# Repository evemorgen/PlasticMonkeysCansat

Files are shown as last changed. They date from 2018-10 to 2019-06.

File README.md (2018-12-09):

# Welcome to Plastic Monkeys - Emergency Beacan repo

Emergency beacan cad render

This is the place where we keep all our work related to Emergency Beacan project.

We are building a CanSat (CanSat is a small soda-sized piece of electronics, created to conduct a scientific mission) equiped with multiple sensors, radio, GPS, thermal camera and screen to provide communication to the victims of natural disasters. Usually, after an earthquake or tsunami, big expeditions and rescue operations take place. Unfortunately they are very often dangerous for rescuers and very expensive. We came up with a solution - instead of people, we can send there many small sats, anyone who finds them can easily send their localization to the rescue center and have a short interview. 

----

## Repo structure

Emergency Beacan is multidisciplinary project involving software, electronics, mechanical design and so on. That being said, there are couple directories covering all mentioned before:

  - [`code`](code/) - keeps all software related stuff
  - [`docs`](docs/) - is the place where we keep project documentation, you might be espetialy interested in our [reports](docs/reports)
  - [`assets`](assets/) - contains all graphical designs regarding our logos and .. assets?
  - [`diagrams`](diagrams/) - all things related to visual representation of conceptual design

----

## Where to find us

We are present in most of modern social media platforms, you can follow us at:
  - our website <http://plastic-monkeys.space>
  - [facebook](https://www.facebook.com/pmcansat/)
  - [instagram](https://www.instagram.com/pmcansat/)
  - [youtube](https://www.youtube.com/channel/UCQk3wuW7xEt5WVLtaiRNTGQ)
  - or write us old fashioned email <hello@plastic-monkeys.space>

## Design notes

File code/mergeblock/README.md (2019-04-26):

# Easy Merge Block

### How to use:
in config.ini specify your settings:  
`output` = path to file where binary ready-to-send packets are going to be stored, will be created if it doesn't exist  
`datalog` = path to file where readable packets are going to be stored, will be created if it doesn't exist  
`sleeptime` = delay before merges  
`line_length` = your maximum line length in sensors' logs - how many bytes script have to load to RAM to load last line  
`text_packets` = yes or no - set to yes if you want to have readable packets  
`exception_sleep_time` = delay after getting an exception  
`packet_length` = number of bytes in output packet  

You also specify paths to all logs that we want to merge in `[PATHS]` section like this:
```
[PATHS]
path1 = foo1.log
path2 = /home/xyz/Desktop/foo2.log
path3 = /home/sensors/temperature/temp.log
```

### Output:
Packet of `packet_length` size in `bytes`:  
one byte describing data_dict size + msgpacked data_dict + fill ('-') to `packet_length`  

### Start:
Next you can run your mergeblock using: `python3 merge.py`  
Libraries used: configparser, msgpack, time, sys, re, logging

### Some additional notes:
Mergeblock takes only last int from sensors' logs' lines: when we have line like this:  
`123 255`  
mergeblock will use only 255 as our value. This approach gives us the ability to add things like timestamps to each reading, that will be ignored by mergeblock, but can be useful after retrieving sd_card with sensors' logs.

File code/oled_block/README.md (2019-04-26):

# OLED_BLOCK

### Get this bad boy working:  
Just follow [this](https://www.raspberrypi-spy.co.uk/2018/04/i2c-oled-display-module-with-raspberry-pi/) tutorial.

### How it works?
Program should have access to oled_buffer.txt file, you can specify the path in the config file.  
It reads a file and converts it into string, ignoring new lines (`'\n'`) and "fillers" (`'-'`).  
After that it splits a message into lines, you can define width of them in config file (recommend 20 for 0.96 inch OLEDs), and prints them.  
It also adds hyphens where it's necessary.  
It repeats the process, with delay equal to `sleep_time` variable specified in config file

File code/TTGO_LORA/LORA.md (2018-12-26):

# LoRa w/ TTGO

Hello, here are some notes about our RaO2 working with TTGO.

## TTGO SETUP

Firstly - our TTGO from Germany is actually called Heltec WiFi LoRa 32

To start working with it you need to add some libraries, it is shown in steps below:

#### Step 1
Erase all old ESP32 Libraries that you've installed before. If you haven't you can skip this step.

#### Step 2
Jump to Arduino IDE, go to File > Preferences > Additional Board Manager URLs, add this line:
`https://dl.espressif.com/dl/package_esp32_index.json`

#### Step 3
Jump to Tools > Boards > Board Manager and search ESP32, next download:
`esp32 by Espressif Systems`

#### Step 4
Go to Library Manager (Open Sketch > Include Library > Manage Libraries) and install:
`LoRa by Sandeep Mistry`

#### Step 5
Install another library from Libraries Manager:
`U8g2`

Alternative Link: [U8g2](https://github.com/olikraus/u8g2)

#### Step 6

Go to Boards and select:
`Heltec_WIFI_LoRa_32`

#### That's it!

## LORA NOTES

In my configuration (Arduino Micro with Ra02 as a TX, Heltec Board as a receiver) it works with best results with:

#### TX
```LoRa.setSpreadingFactor(7)
LoRa.setTxPower(20); //TX Power
int delayTime = 100; //Time between sending packets
```

Coding Rate and Spreading Factor are responsible for data transfer speed. However Coding Rate is set to the best value
By default, Spreading factor is the better the lower. Unfortunately as you can read here: [LoRa Library API](https://github.com/sandeepmistry/arduino-LoRa/blob/master/API.md)
Spreading Factor lower than 7 requires an implicit header mode. You can start it by:
`LoRa.beginPacket(implicitHeader);`

But then TTGO (RX) starts to loose about half of packets, making data transfer actually worse than with Sprading Factor = 7.
Also the BAND 433E6 is the best one && LoRa with Arduino needs around 1A power supply to provide the best results.

I didn't change anything in RX, there's not much to tinker around. It just mustn't clear the display very often - it is so slow,
that TTGO misses all packets during this proccess. What's important about TTGO is that its OLED run on SPI, pinout is
pretty weird and writing code for OLED Screen from scratch can be quite hard. I strongly suggest using code that is in this repo.

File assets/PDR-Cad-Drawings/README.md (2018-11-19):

# Images provided with files:  
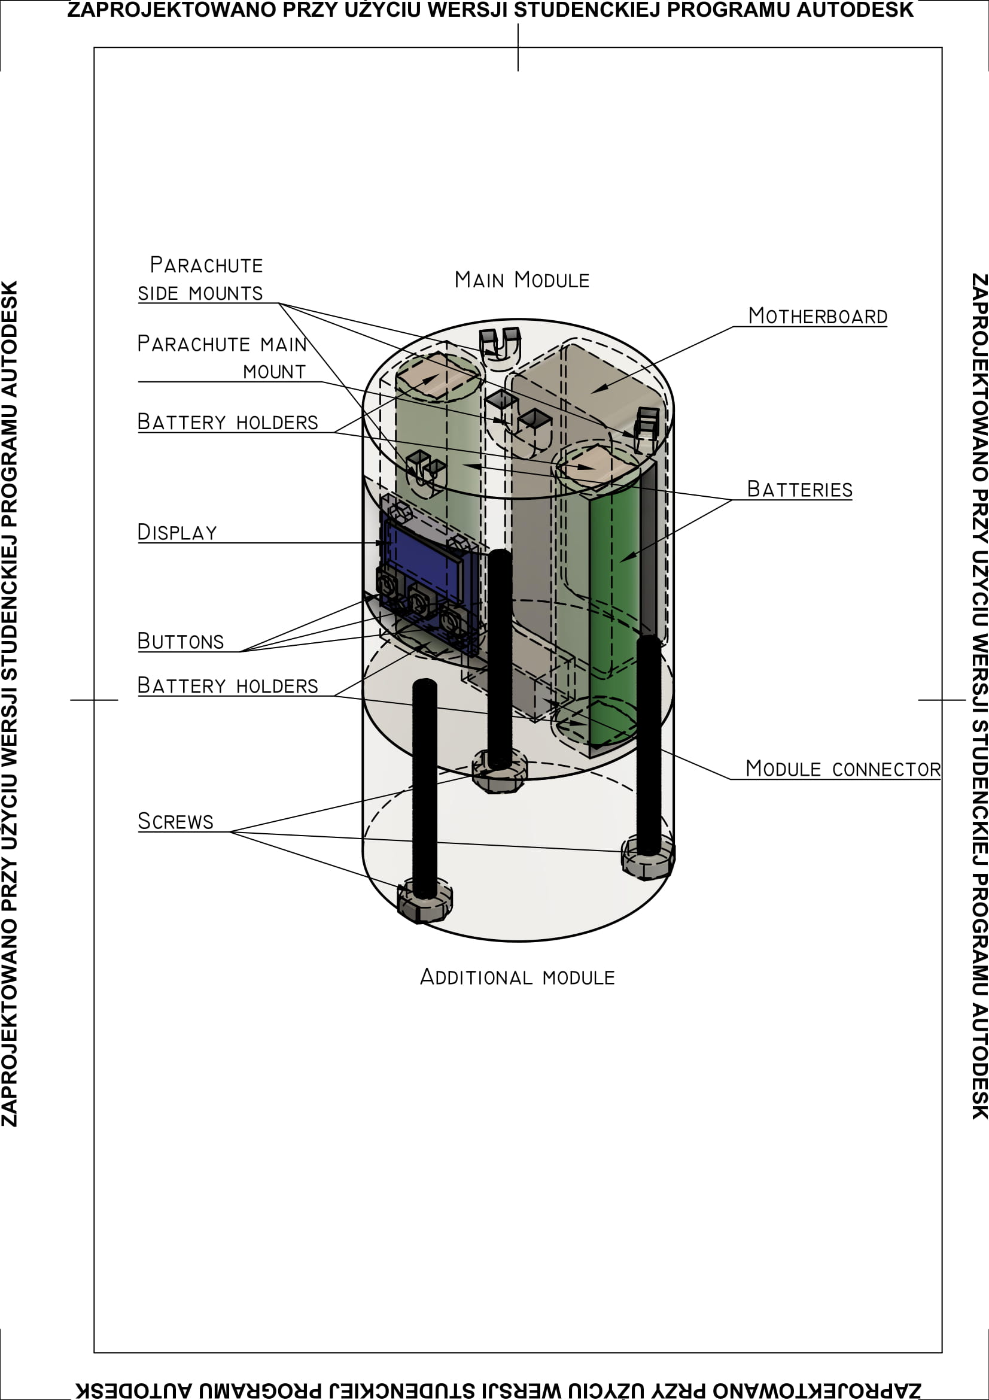
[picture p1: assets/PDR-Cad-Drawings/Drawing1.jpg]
  
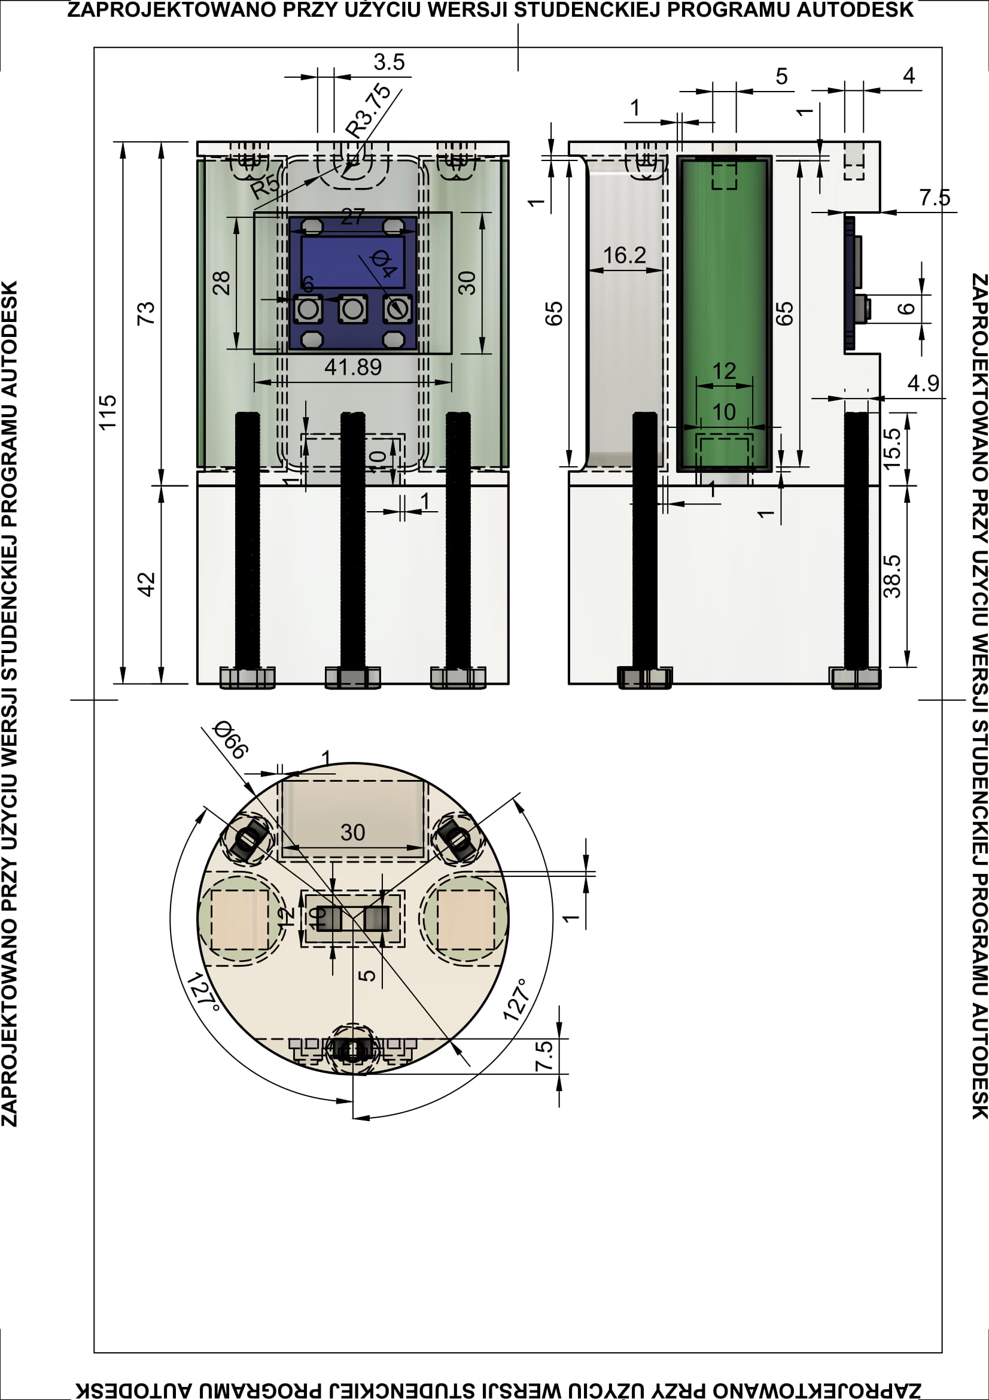
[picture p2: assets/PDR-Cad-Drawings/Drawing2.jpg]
  
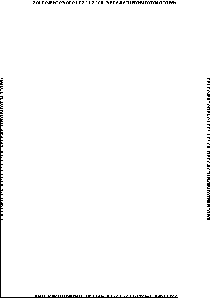
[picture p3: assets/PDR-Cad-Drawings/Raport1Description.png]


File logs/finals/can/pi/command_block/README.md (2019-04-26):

# Command Block

#### Requirements:
  Needs config.ini with specified:  
  `camera_log_file` - file where photos' timestamps appear  
  `thermal_log_file` - file where thermal photos' timestamps appear  
  `oled_text_buffer` - file from which the text will be read on OLED, and where we will append text  
  `lora_status_file` - file where lora commands will appear  
  `rx_file` - file with recieved string-packets to process  
  `sleep_time` - delay time in seconds (float) between processing new messages  
  `exception_sleep_time` - delay time in seconds (float) after getting a exception  
  `packet_line_length` - length of a packet, at least 7  
  `time_stamp_length` - number of characters used in packet to describe a timestamp  

  ##### Note:
  First character in each packet should be a one char header!

#### How it works:
  Each sleep_time command_block reads the recent recieved packet from the rx_file if new line popped in. After that it analyzes the first charachter (line[0]) in the packet. Afterwards, it runs a adequate function.
  
#### Command headers:

  ##### I
  Request for a regular image from camera. Requires a destinated timestamp at `line[1]` - `line[timestamp_length]` and quatlity at `line[timestamp_length+1]`
  ##### T
  Request for a thermal image from camera. Requires a destinated timestamp at `line[1]` - `line[timestamp_length]`  
  ##### R
  Checks `line[0]` - `line[5]` for `'REBOOT'` command. Request for a reboot. Requires command_block running as a root
  ##### S
  Request for a system info. Sends back cpu usage, battery percentage, free disk space
  ##### A
  Appends text from a packet from `line[1]` to `line[packet_line_length-1]` to oled Screens buffer.
  ##### C  
  Clears oled buffer

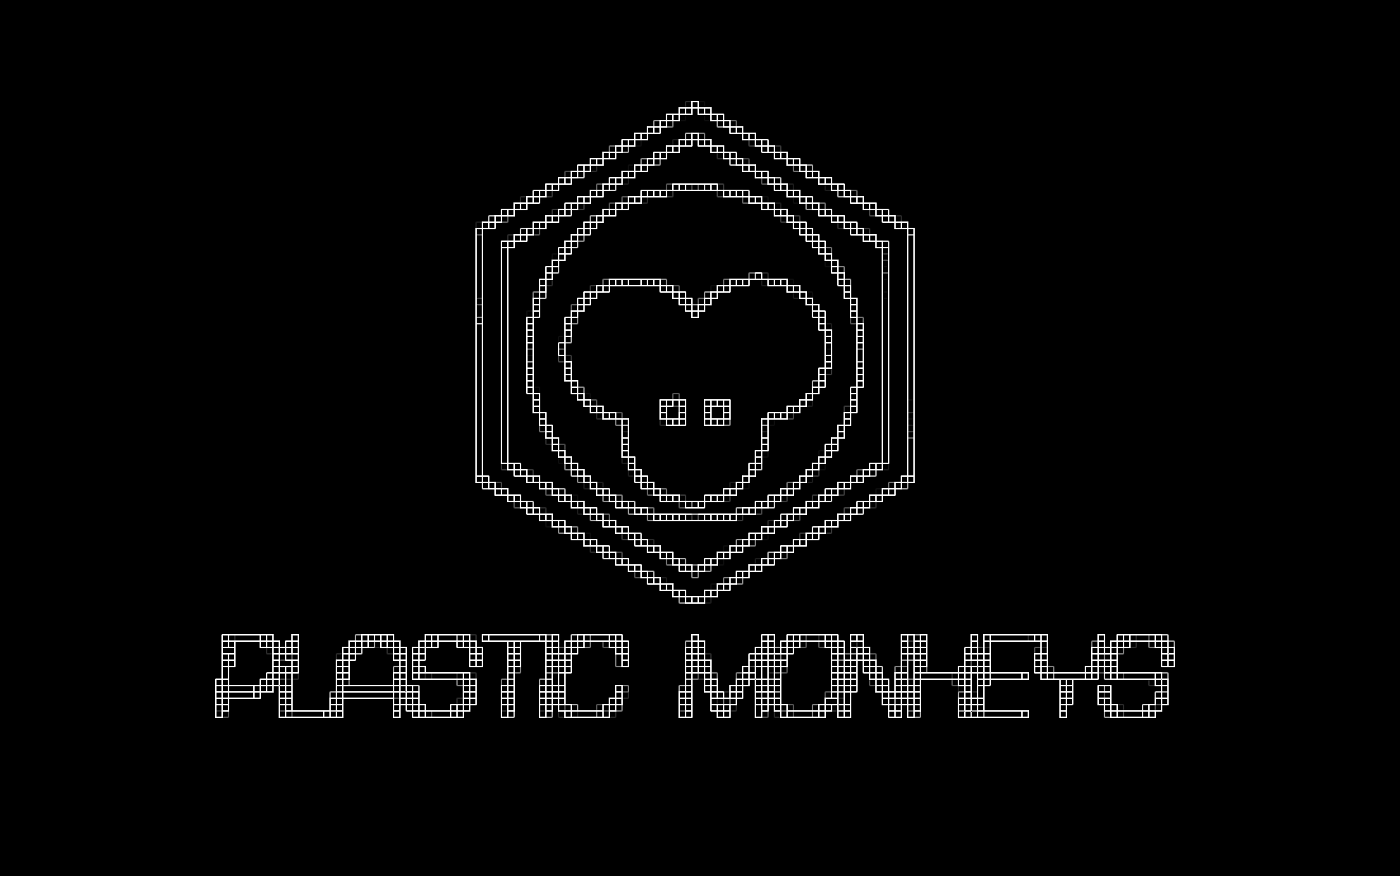
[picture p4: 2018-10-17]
assets/wallpaper-graphics/wallpaper2.png

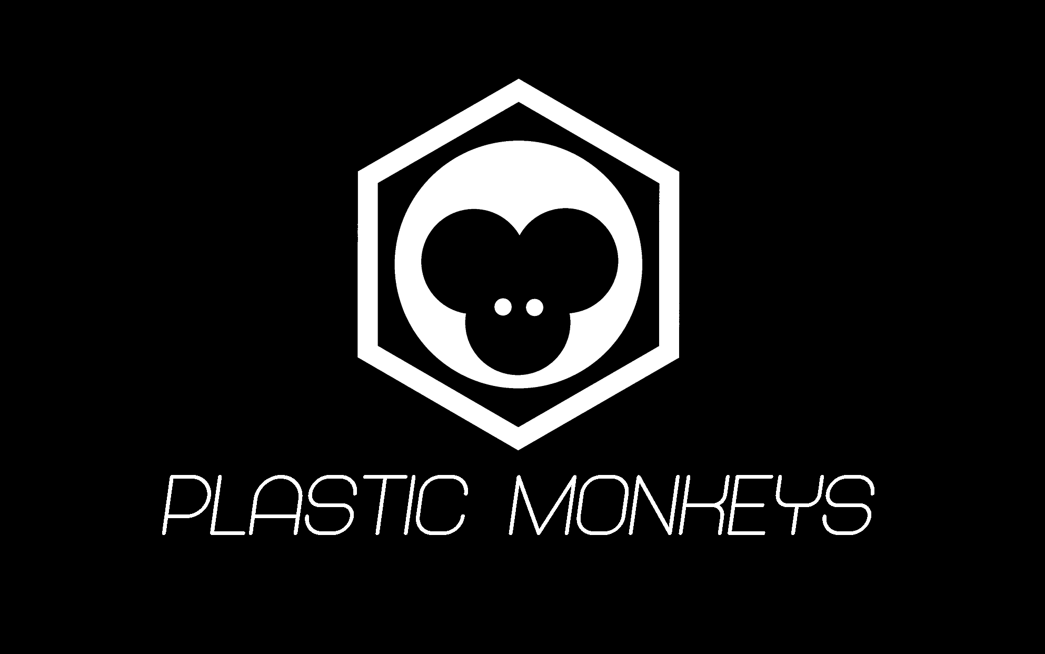
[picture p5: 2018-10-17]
assets/wallpaper-graphics/wallpaper.png

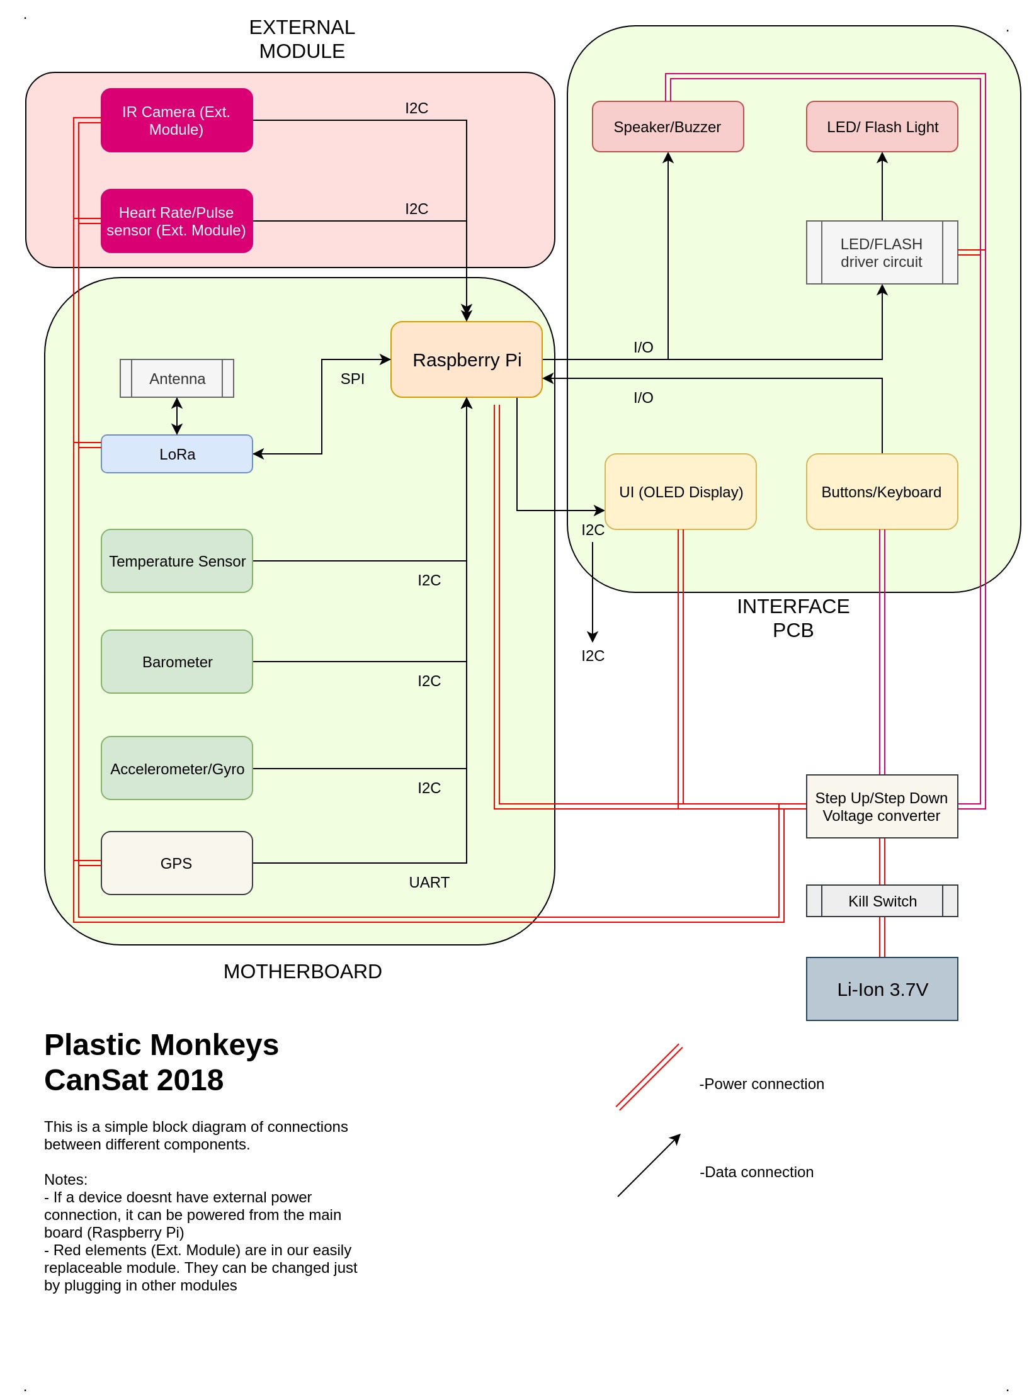
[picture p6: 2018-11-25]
diagrams/report_diagrams/electronicDiagram.jpg

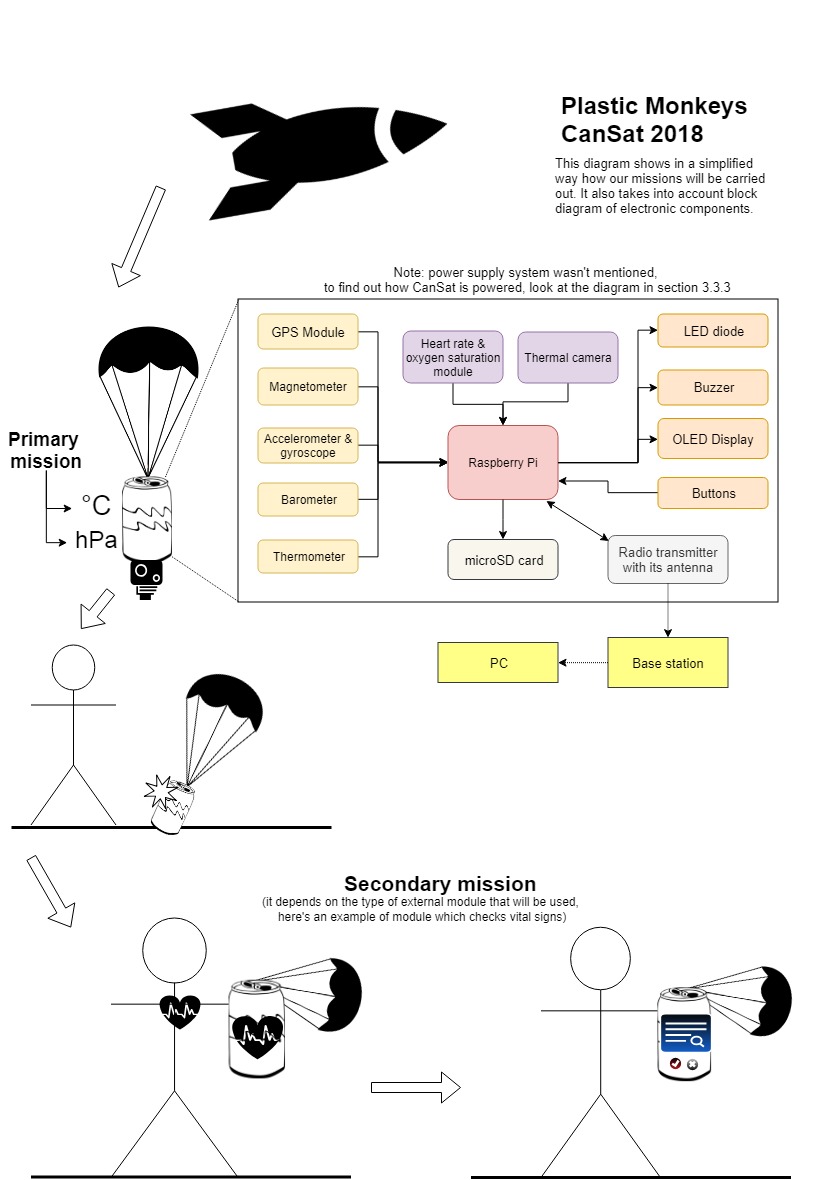
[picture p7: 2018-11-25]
diagrams/report_diagrams/missionDiagram.jpg

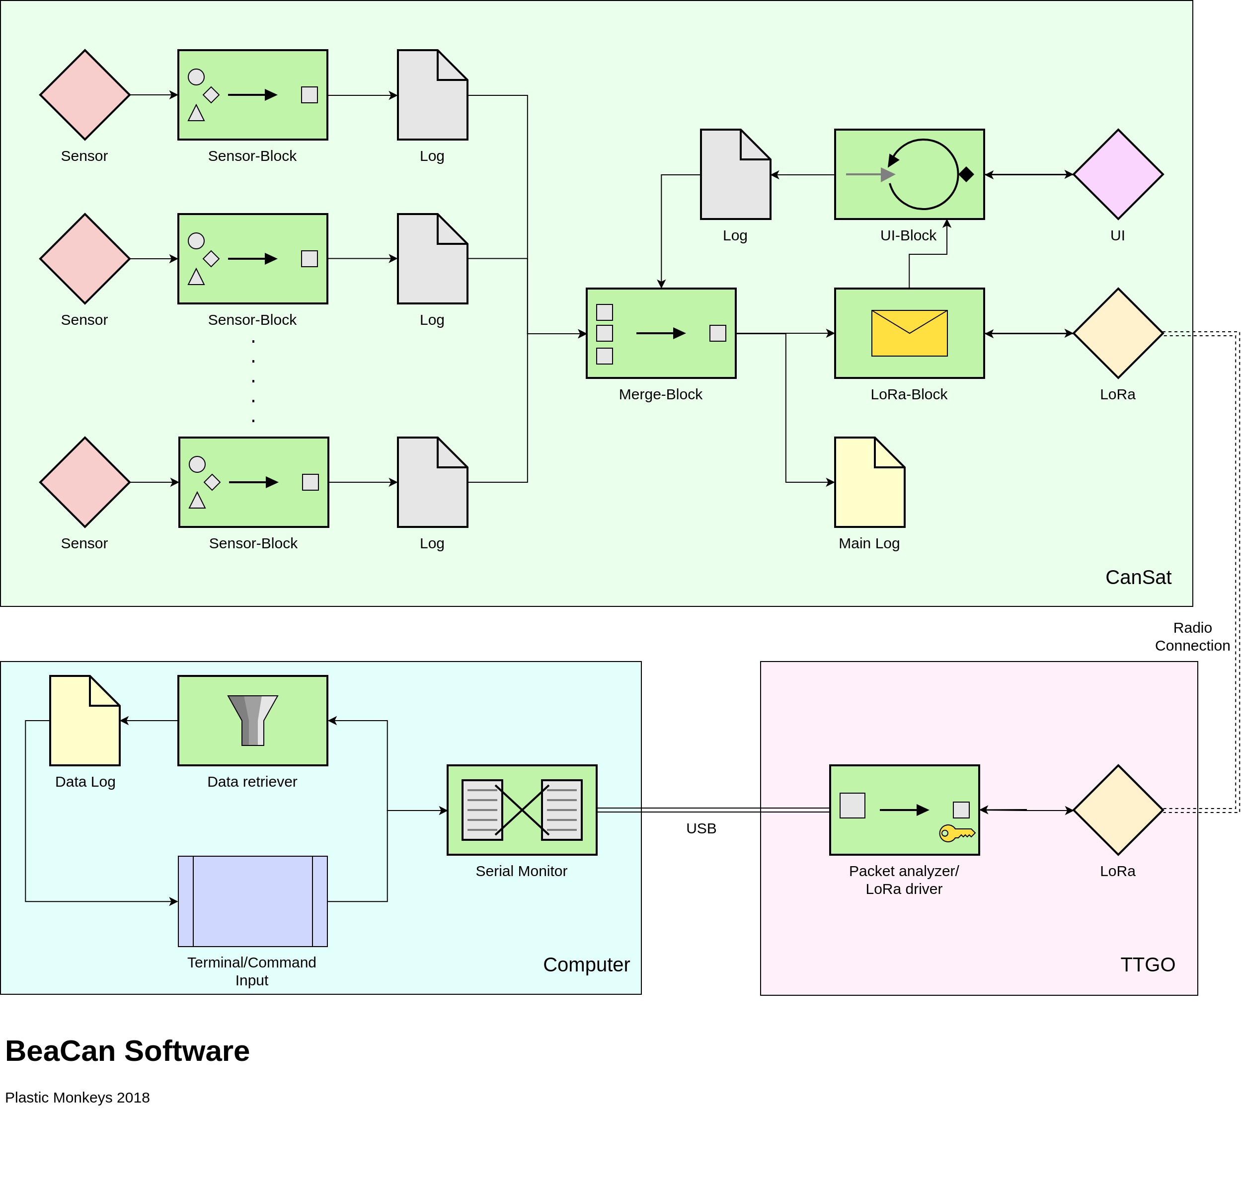
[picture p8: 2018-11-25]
diagrams/report_diagrams/softwareDiagram.jpg

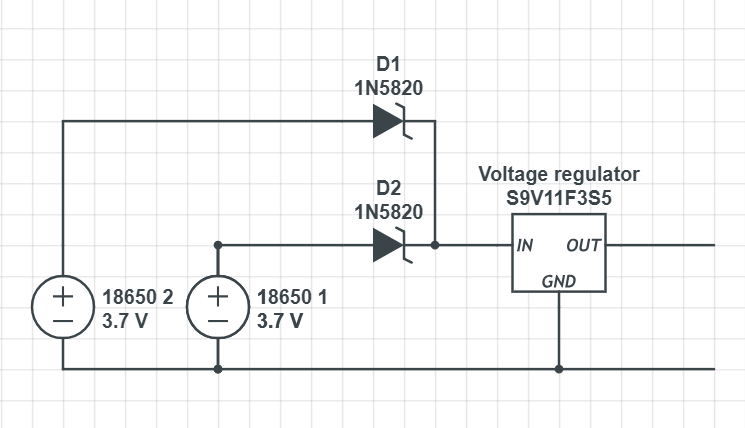
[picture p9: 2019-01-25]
diagrams/report_diagrams/voltageRegulator.png

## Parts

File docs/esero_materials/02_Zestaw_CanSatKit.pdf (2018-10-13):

# Zestaw CanSat Kit

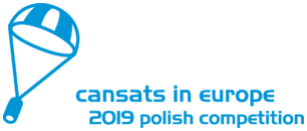
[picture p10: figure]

WARSZTATY CANSAT

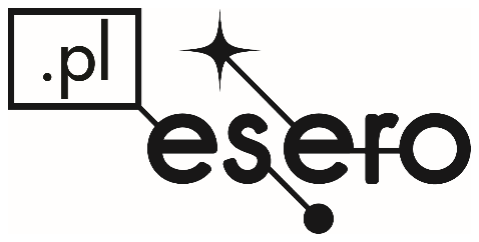
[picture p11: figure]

# Zestaw startowy CanSat Kit

- CanSat Kit rev. 1.1 - https://github.com/CanSatKit
- Podstawowe podsystemy elektroniczne do CanSata i stacji naziemnej
- Pozwala na realizację misji podstawowej
- Stanowi bazę do realizacji misji zaawansowanej
- Prace można rozpocząć praktycznie od razu

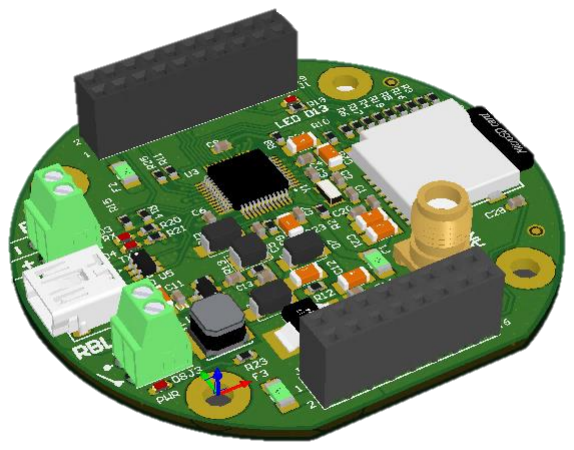
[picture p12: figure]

# Co zawiera zestaw startowy CanSat Kit

### 2 x płytka główna CanSata / stacji naziemnej

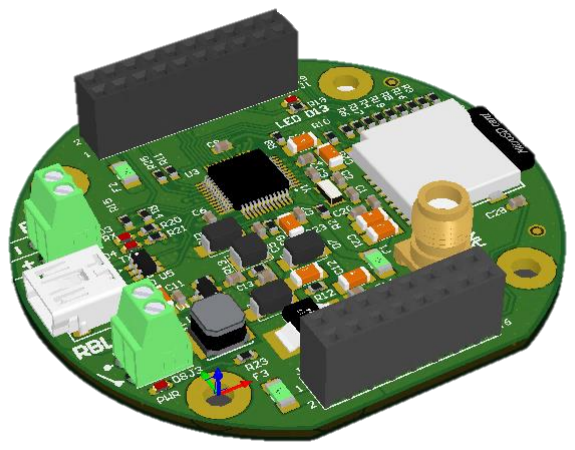
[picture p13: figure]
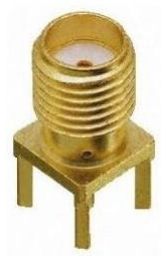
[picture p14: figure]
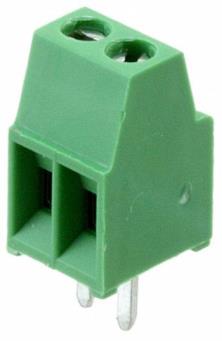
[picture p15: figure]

Akcesoria do płytki głównej:
- złącze antenowe SMA
- złącza typu terminal block do

podłączenia zasilania

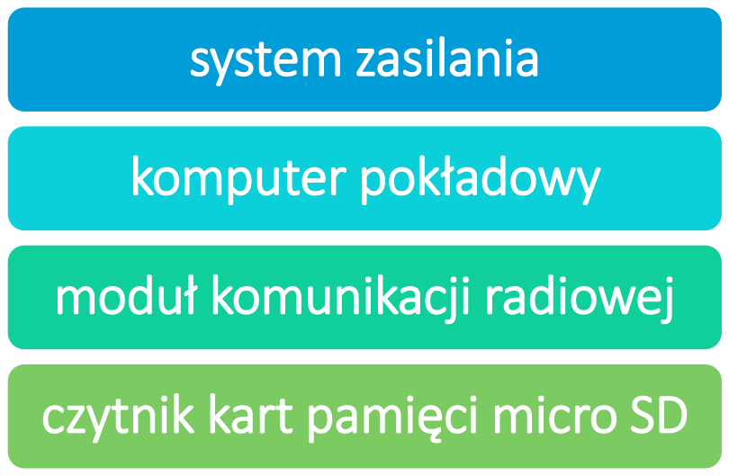
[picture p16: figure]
system zasilania; komputer pokładowy; moduł komunikacji radiowej; czytnik kart pamięci micro SD

# Co zawiera zestaw startowy CanSat Kit

## płytka prototypowa

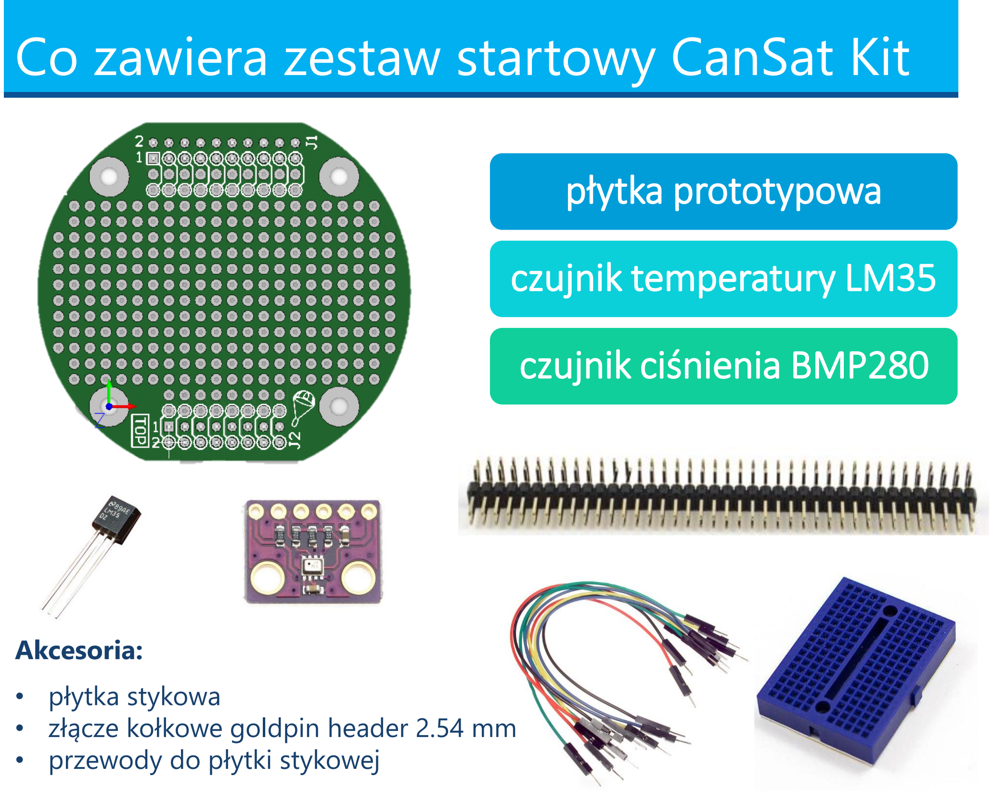
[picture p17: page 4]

## czujnik temperatury LM35

## czujnik ciśnienia BMP280

Akcesoria:

- płytka stykowa
- złącze kołkowe goldpin header 2.54 mm
- przewody do płytki stykowej

# Dokumentacja zestawu

CanSat Kit rev. 1.1 - https://github.com/CanSatKit

## - Biblioteki programistyczne

## - Instrukcje użytkowania

## - Dokumentacja techniczna

## - Schematy i mozaiki płytek PCB

## - Modele 3D płytek

## Ceny elementów zestawu CanSat do budżetu

## Jeśli drużyna używa elementów zestawu CanSat Kit

## dostarczonego przez ESERO w budżecie projektu należy

## przyjąć następujące kwoty:

## - płytka główna: 150 zł

## - czujnik temperatury LM35: 5 zł

## - czujnik ciśnienia BMP280: 10 zł

## - płytka prototypowa: 20 zł

Pozostałe elementy zestawu jak złącza i inne akcesoria można pominąć.

# Zestaw równoważny


- Arduino M0 (lub podobne z SAM21D)
- transceiver radiowy SX127x/RFM9x
- czujnik ciśnienia BMP280
- czujnik temperatury LM35
- czytnik kart micro SD

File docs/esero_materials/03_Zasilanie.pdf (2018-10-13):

# System zasilania


WARSZTATY CANSAT


# System zasilania CanSata

### - „Zasilone urządzenia elektryczne działają lepiej.”

### - Bez dobrego, odpowiednio przetestowanego systemu zasilania nie zadziała nawet najlepiej przygotowana misja!

źródła energii | włącznik główny

# Wymagania konkursowe

### 1. Czas pracy CanSata na bateriach

- minimalny czas pracy¹
: 4 godziny
- rekomendowany¹
: 6 godzin

### 2. Łatwa dostępność baterii i sposób wymiany

- nawet przy zastosowaniu akumulatorów

### 3. Włącznik główny

- wskazane, aby odcinał całkowicie zasilanie CanSata
- musi wyłączać wszelkie transmisje radiowe
- łatwo dostępny, obsługiwany przez organizatorów

1 czas działania dotyczy misji podstawowej

# Wymagania konkursowe

### 4. Niedozwolone jest użycie akumulatorów litowo-

polimerowych (Li-pol, Li-Po)

- ze względu na zagrożenie pożarowe
- akumulatory litowo-jonowe (li-ion) są dobrą alternatywą

# System zasilania płytek CanSat Kit

### 3.3 V

### 5 V


dystrybucja na płytce i zasilanie:
- mikrokontrolera,
- modułu radiowego,
- karty microSD

dla użytkownika

lub

Vbat¹

1 Vbat dostępne tylko wtedy, gdy podłączona jest bateria lub akumulator

# Źródła zasilania

### 1. Port mini USB

- niepolecane dla CanSata, ale polecane dla stacji naziemnej
- zasilanie z komputera, smartphone’a, power-banka

### 2. Wejście na baterie / akumulatory – złącze BAT (J4)

- najlepsze rozwiązanie do zasilenia CanSata


# Kompatybilne baterie i akumulatory

Napięcie zasilania CanSat Kit (złącze BAT)

- dopuszczalny zakres: 2.5 – 4.5 V
- optymalizowane dla akumulatorów litowo-jonowych 3.7 – 4.3 V

Czym kierować się przy wyborze baterii/akumulatorów?

- napięcie (można też łączyć szeregowo)
- wydajność prądowa
- pojemność (wyrażana w mAh/Ah/Wh)
- baterie jednorazowego użytku lub ładowalne akumulatory
- wymiary, masa, kształt
- sposób montażu

# Kompatybilne baterie i akumulatory

Baterie typu AAA/AA/R14

- popularne „paluszki”
- cynkowo-węglowe i alkaiczne


- 1.5 V każde ogniwo – 3 x 1.5V = 4.5 V

Akumulatory typu AAA/AA/R14

- popularne „akumulatorki”
- Ni-Cd lub Ni-MH
- 1.2 V każde ogniwo – 3 x 1.2V = 3.6 V

Uwaga na sprężyny w koszyczkach na ogniwa! Możliwe rozłączenie podczas startu rakiety!

# Kompatybilne baterie i akumulatory


Akumulatory litowo-jonowe (li-ion)

- popularne (telefony, tablety, laptopy)
- wielokrotnego użytku
- bardzo dobry stosunek pojemność/wymiary/masa
- 3.7 V każde ogniwo – kit zoptymalizowany pod li-ion
- wiele rozmiarów i pojemności:

# Kompatybilne baterie i akumulatory


Mocowania i pojemniki na akumulatory li-ion

# Niekompatybilne baterie i akumulatory


Akumulatory litowo-polimerowe (li-pol, li-po)

- niedozwolone do użytku w konkursie
- niebezpieczne w przypadku uszkodzenia lub zwarcia

Baterie litowe

- napięcie 3 V
- oferują dużą pojemność ale przy bardzo niewielkich prądach rozładowania – CanSat pobiera znacznie więcej!

# Budżet energii

step-up
converter
5 V

regulator
liniowy
3.3 V

radio
mikrokontroler
karta micro SD

czujnik ciśnienia

czujnik temperatury


2.5 – 4.5 V

### Jaką moc urządzenia pobierają z baterii – przykład:

- z linii 5 V urządzenie pobiera prąd I5V = 0.1 A, P5V = I ⋅ U = 0.1 ⋅ 5 = 0.5 W
- z baterii pobiera zatem Pbat = P5V/η5V = 0.5/0.8 = 0.625 W
- z linii 3.3 V urządzenie pobiera I3.3V = 0.1 A, P3.3V = 0.1 ⋅ 3.3 = 0.33 W
- z baterii pobiera zatem Pbat = P3.3V/(η3.3V ⋅ η5V) = 0.33/(0.8 ⋅ 0.66) = 0.625 W
- sumarycznie oba urządzenia pobierają z baterii 1.25 W

sprawność
sprawność | η= 66%
η= 80%

# Studium przypadku – budżet energii

Budżet energii CanSata Demo

step-up converter 5 V; regulator liniowy 3.3 V; radio; mikrokontroler; karta micro SD; czujnik ciśnienia; czujnik temperatury; kamera; GPS; sprawność

### 1. Sprawdzamy średnie zużycie energii przez każde z urządzeń –

albo w dokumentacji producenta, albo poprzez pomiar amperomierzem

# Studium przypadku – budżet energii

Budżet energii CanSata Demo

# | urządzenie | średni pobór prądu [mA] | Napięcie zasilania [V] | η | Moc pobierana z baterii [mW]

1 | komputer pokładowy | 20 | 3.3 | 0.5 | 132
2 | moduł radiowy SX1278 | 90¹ | 3.3 | 0.5 | 594
3 | GPS | 35 | 3.3 | 0.5 | 231
4 | czujnik ciśnienia BMP280 | 1 | 3.3 | 0.5 | 7
5 | czujnik temperatury LM35 | 1 | 5 | 0.8 | 6
6 | kamera | 150 | 5 | 0.8 | 938
Sumaryczny pobór mocy z baterii: | 1908

1 moduł radiowy SX1278 pobiera 120 mA podczas nadawania, średnio nadaje tylko przez 75% czasu, dlatego średni pobór prądu to 90 mA

# Studium przypadku – budżet energii

Budżet energii CanSata Demo

Sumaryczny pobór mocy z baterii: ~ 1900 mW

Pojemność akumulatora wymagana dla 6 godzin pracy:

Ebat = P ⋅ t = 1900 | mW | ⋅ 6 | h | = 11400 mWh

Jak przeliczać pojemność akumulatorów?


Ebat = 900 | mAh | ⋅ 3.7 | V | = 3330 mWh

# Studium przypadku – budżet energii

Budżet energii CanSata Demo

- potrzebna energia: 11400 mWh
- 4 akumulatory li-ion 18350 połączone równolegle


- każdy o pojemności 900 mAh @ 3.7 V co daje 3330 mWh
- połączone razem w baterię czeterech akumulatorów

pojemność wynosi: 4 x 3330 mWh = 13320 mWh

## Studium przypadku – budżet energii - testy

### Budżet mocy jest ważny, ale nie zastąpi testów!


# Włącznik główny

- Odporność na przypadkowe przełączenie się podczas lotu w rakiecie, opadania lub lądowania!
- Łatwa dostępność - po lądowaniu CanSata organizatorzy wyłączą go za pomocą głównego przełącznika

– CanSat musi przynajmniej zaprzestać nadawać sygnał radiowy


# Włącznik główny - podłączenie


Zasilanie ze złącza BAT (J4) jest doprowadzone tylko, gdy zwarte jest złącze włącznika głównego RBL (J3)!

# Studium przypadku – przełącznik RBL


# Studium przypadku – przełącznik RBL


# Testy i przewidywanie problemów

### 1. Jak długo CanSat jest w stanie realizować swoją

misję?

### 2. Jak długo CanSat będzie nadawał sygnał

radiowy?

### 3. Jak prawdopodobne jest samoczynne

przełączenie włącznika głównego? W jakich warunkach?

### 4. Do zastanowienia się:

Jakie jeszcze testy systemu zasilania można wykonać?

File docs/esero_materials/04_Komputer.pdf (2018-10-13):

# Komputer pokładowy


WARSZTATY CANSAT


# Komputer pokładowy


- mikrokontroler Atmel ATSAMD21G18
- kompatybilny z Arduino M0
(lub podobnymi z SAM21D)
- port mini USB
programowanie + SerialUSB + zasilanie
- wyprowadzone piny procesora (m.in. GPIO, ADC, DAC, SPI, I2C, UART)


- wejścia/wyjścia mikrokontrolera
w standardzie 3.3 V! Podłączenie wyższego napięcia może skutkować nieodwracalnym uszkodzeniem!

# Złącza komputera pokładowego


# Złącza komputera pokładowego

20


19

2

1

UWAGA! – Wystąpił błąd w opisie złącza J1 od dolnej strony płytki! Szczegóły na następnym slajdzie lub w dokumentacji kitu!

## Złącza komputera pokładowego - errata

20


19

2

1

Jak pokazano na powyższym obrazku piny złącza J1 zostały błędnie ponumerowane na opisie płytki od strony dolnej (bottom). Numeracja od strony górnej (top) jest prawidłowo oznaczona. Pole pinu nr 1 ma zawsze kształt kwadratowy.
Nazwy pinów np. GND, AREF, 5V itd. są prawidłowe i w prawidłowych miejscach!

np.:
pin nr 1 – 5 V
pin nr 3 – SCL

pin nr 19 – AREFA
pin nr 20 – GND

# Komputer pokładowy – porty

Wejścia/wyjścia cyfrowe

- włączanie/wyłączanie np. diod LED i innych urządzeń
- odczytywanie stanu wejścia – np. możliwe podłączenie przełączników

Wejścia analogowe

- pomiar napięcia (woltomierz): 0 – 3.3 V, rozdzielczość 0.81 mV
- czujniki analogowe (np. czujnik temperatury z zestawu)

Wyjścia analogowe (PWM lub DAC)

- generowanie napięcia, sygnału analogowego (np. sygnał dla brzęczyka)

# Komputer pokładowy – porty

Serial port (UART)

- dwustronna komunikacja pomiędzy Arduino, a urządzeniami zewnętrznymi
- np. odbiorniki GPS, czujniki, komunikacja Arduino-komputer (SerialUSB)

I2C

- cyfrowy interfejs komunikacyjny
- czujniki cyfrowe (np. czujnik ciśnienia), pamięci, itp.

SPI

- cyfrowy interfejs komunikacyjny
- czujniki cyfrowe, pamięci (np. karta SD), moduły radiowe, itp.

# Ekosystem Arduino


# Programowanie – Arduino IDE


- multiplatformowe środowisko
(Windows, Linux, Mac OS)
- programy w języku C++
- kompilator i programator
- biblioteki Arduino do obsługi płytek Arduino oraz urządzeń zewnętrznych
- wbudowana baza przykładów
- przydatne narzędzia:
monitor portu szeregowego, kreślarka (Serial Plotter)

# Uruchomienie płytki

### Cała procedura: rozdział 5. dokumentacji: Uruchomienie zestawu

1. Podłącz płytkę przez USB do komputera
2. Uruchom Arduino IDE
3. Wybierz model płytki: Arduino M0


# Uruchomienie – instalacja bibliotek


4. Instalacja bibliotek programistycznych CanSat Kit:

1

2

3

# Uruchomienie płytki

5. Wybierz port COM pod którym wykryta jest płytka:


UWAGA! Numer portu COM może się zmieniać po wgrywaniu programu, resetowaniu komputera!

# Wgrywanie pierwszego programu

- Otwórz przykład „HelloCanSat” z menu „Plik -> Przykłady -> CanSat Kit Library”
- skompiluj i wgraj program do mikrokontrolera:


# Program HelloCanSat!

dane; SerialUSB; Serial Monitor; „x. Hello CanSat!”
1 sekunda; LED 13; (pin D13)

# Program HelloCanSat!


# Podsumowanie

## Gdzie jesteśmy?

✓ zainstalowane sterowniki do płytki

✓ skonfigurowane środowisko programistyczne (Arduino IDE)

✓ gotowa do pracy płytka komputera pokładowego

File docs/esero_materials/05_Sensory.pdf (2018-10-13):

# Czujniki


WARSZTATY CANSAT


Czujniki (sensory) - przetworniki wielkości nieelektrycznych na elektryczne np. temperatura na napięcie.

## Czujniki - czyli jak rozpoznać środowisko

mierzona; wielkość; sensor; sygnał elektryczny; układ elektroniczny

# Rodzaje pomiarów

czujnik temperatury | temperatura
czujnik ciśnienia | ciśnienie

## temperatura ciśnienie

## wysokość

Pomiary bezpośrednie


Pomiary pośrednie

## Czujnik ciśnienia atmosferycznego BMP280


- Zakres pomiaru ciśnienia: 300 - 1100 hPa (wysokość 9000 m – -500 m)
- Maksymalna rozdzielczość: 0.16 Pa (< 10 cm)
- Zasilanie: 3.3 V
- Interfejs komunikacji: I²C (adres: 0x76)

# Magistrala I²C


# BMP280 – podłączenie

### 1. Podłącz czujnik ciśnienia do płytki CanSat Kit w następujący sposób:

Piny płytki CanSat Kit | Piny czujnika ciśnienia BMP280
+3.3 V | VCC
GND | GND
SCL | SCL
SDA | SDA

Wszelkie podpięcia/zmiany w podłączeniu elementów wykonuj przy odłączonej płytce od źródeł zasilania (port USB, baterie)!
Sprawdź poprawność podłączenia i dopiero wtedy włącz zasilanie!

Wykorzystaj płytkę stykową oraz kabelki do płytki stykowej.

# BMP280 – oprogramowanie

2. Otwórz przykładowy program „File -> Examples -> CanSatKit -> PressureSensor” i wgraj go na płytkę.
3. Uruchom Serial Monitor (Monitor portu szeregowego)
4. Uruchom aplikację Serial Plotter (Kreślarka)


# Analogowy czujnik temperatury LM35


- czujnik analogowy – wykorzystamy pomiar

napięcia (przetwornik ADC) w komputerze

pokładowym

- liniowa zależność napięcia wyjścia

od temperatury:

UWY T = 10 | mVൗ℃ | ⋅ T [℃]
- rozdzielczość pomiaru napięcia przez komputer pokładowy ≈ 0.81 mV - daje to ~ 0.1 ℃ rozdzielczości
- dokładność czujnika 0,5 ℃ @ 25 ℃

# LM35 - podłączenie


Piny płytki CanSat Kit | Piny czujnika temperatury LM35
+5 V | (1) Vcc
A0 | (2) OUT
GND | (3) GND

Wszelkie podpięcia/zmiany w podłączeniu elementów wykonuj przy odłączonej płytce od źródeł zasilania (port USB, baterie)!
Sprawdź poprawność podłączenia i dopiero wtedy włącz zasilanie!

Wykorzystaj płytkę stykową oraz kabelki do płytki stykowej.

# LM35 – oprogramowanie

1. Otwórz przykładowy program „File -> Examples -> CanSatKit -> TemperatureSensor” i wgraj go na płytkę.
2. Uruchom Serial Monitor (Monitor portu szeregowego)
3. Uruchom aplikację Serial Plotter (Kreślarka)


# LM35 – praktyczne porady

1. W celu poprawy jakości wskazań czujnika (redukcji szumów) zastosuj prosty filtr dolnoprzepustowy zbudowany z kondensatora i rezystora
2. Możesz mierzyć wskazanie czujnika kilka razy (pomiar jest bardzo szybki), a następnie uśrednić wynik w celu uzyskania lepszej jakości pomiaru
3. Jeśli czujnik wskazuje „na oko” za wysoką lub za niską temperaturę możesz spróbować go skalibrować (jego tzw. offset) – użyj do tego innego termometru (referencyjnego) lub innych metod (pomyśl nad nimi!)

# Czujniki analogowe vs. cyfrowe

Drużyny mają pełną dowolność w wyborze modeli czujników także tych do misji podstawowej!

## analogowe

### - często uproszczone oprogramowanie

### - większa podatność na szumy

### - podłączamy do pinów Ax

## cyfrowe

### - bardziej skomplikowane oprogramowanie

### - bardziej odporne na szumy

### - wiele czujników na jednej magistrali (I2C, SPI)

# Płytka ładunku użytecznego (payload)


# Umiejscowienie czujników


Misja podstawowa zakłada pomiar temperatury powietrza na
zewnątrz CanSata!

# Przetwarzanie danych

Lepiej unikać obróbki danych na pokładzie CanSata

w miarę możliwości i użyteczności lepiej przesyłać wartości „surowe”

np. wysokość (h) obliczana ze wzoru barometrycznego:

### p = p0 ⋅ exp −

### μgℎ

RT

p0 – ciśnienie atmosferyczne na poziomie odniesienia,

μ – masa molowa powietrza,

g – przyspieszenie ziemskie,

R – stała gazowa,

T – temperatura powietrza w K.

# Analiza danych

- Co mówią zebrane dane?
- Dopasowanie przewidywań teoretycznych / modelu
- Określenie poprawności danych
- Jak najlepiej przedstawić zebrane dane?
– tabela | – wykres
- Wykresy do misji podstawowej:
– w funkcji czasu: np. T(t), h(t)
– w funkcji innych wielkości: np. T(h)

# Wizualizacja i obróbka danych

- SerialPlot
- pakiety biurowe np. LibreOffice, MS Office itp.
- GNUPlot
- Python
- LabVIEW
- Matlab / Octave

# Jak narysować wykres?

Altitude [m]; Time [s]

Altitude vs. Time

Data from pressure sensor
Data from GPS

Lack of GPS data

# Jak wizualizować dane?


Lack of GPS data

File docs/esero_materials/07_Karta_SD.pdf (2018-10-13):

# Redundancja danych


WARSZTATY CANSAT


# Redundancja danych – karta SD

- Łącze radiowe jest zawodne
- Warto zabezpieczyć się zapisując dane w samym CanSacie, tak aby odzyskać je po lądowaniu


- W pamięci CanSata można też zapisać większą ilość danych (np. częściej próbkować czujniki)
- Płytka główna CanSat Kit zawiera w sobie złącze na karty micro SD podłączone do mikrokontrolera interfejsem SPI

# Redundancja danych – karta SD

- dostępna biblioteka do użycia kart SD z Arduino
- przykład Datalogger


# Redundancja danych – karta SD

- Szczegółowe informacje w rozdziale „5.6 Używanie karty micro SD” dokumentacji zestawu CanSat Kit
- Dodatkowa dokumentacja:
- https://www.arduino.cc/en/Reference/SD
- https://www.arduino.cc/en/Tutorial/ReadWrite
- https://www.arduino.cc/en/Reference/SDCardNotes

Praktyczne wskazówki

- używaj kart o stosunkowo niewielkiej pojemności < 32 GB
- karta powinna być sformatowana na system plików FAT16 (ew. FAT32)
- zapisywane pliki muszą mieć nazwę w formacie 8.3 czyli maksymalnie 8 znaków nazwy, 3 znaki rozszerzenia np.: cansat.txt
- używaj metody flush(), aby uniknąć utraty danych

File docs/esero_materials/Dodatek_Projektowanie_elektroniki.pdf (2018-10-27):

# Projektowanie elektroniki

WARSZTATY CANSAT


# Od pomysłu, do układu

Projektowanie układów to


skomplikowany i czasochłonny proces.

Rozbicie go na poszczególne etapy, może znacznie uprościć zadanie.

- pomysł
- projekt
- testy prototypu
- ewentualne poprawki
- wykonanie modelu końcowego
- testy

# Określenie funkcjonalności układu


- Jakie funkcje ma spełniać układ?
- Z czym ma współpracować (być połączony)?
- Jakie mamy zasoby:
- technologiczne
- finansowe
- ludzkie

# Schemat elektroniczny


- schemat zawiera symbole
wszelkich części elektronicznych
- programy do rysowania
schematów: Eagle, KiCad EDA

# Prototypowane


- elektronika czasem bywa
nieprzewidywalna
- płytki prototypowe umożliwiają łatwe i szybkie sprawdzenie poprawności działania obwodu

# Prototypowane


- wiele elementów istnieje w różnych obudowach, co umożliwia np. prototypowanie na obudowach THT, a finalnie użycie elementów SMD

# Określenie technologii wykonania


- płytki prototypowe
- obwody drukowane PCB

# Płytka uniwersalna (prototypowa)


- różne rodzaje płytek
- w zależności od potrzeb
- oprogramowanie typu Fritzing ułatwia proces projektowania

# Określenie technologii wykonania

- płytki prototypowe
- obwody drukowane PCB

# Tworzenie obwodu drukowanego


- stworzenie mozaiki ścieżek na podstawie schematu

edytor schematu i PCB w jednym programie

# Tworzenie obwodu drukowanego


# Tworzenie obwodu drukowanego


- wymaga pewnego
doświadczenia (kilku prób)
- dużo tutoriali dostępnych w Internecie
- niewielkie koszty
- niezbyt czasochłonne
- możliwość zrobienia dużo bardziej skomplikowanej płytki
- dużo lepsza jakość wykonania
- łatwiejsze lutowanie i
niezawodność
- długi czas oczekiwania
- wyższa cena

# Lutowanie


- lutowanie potrzebuje czasu:
- nagrzanie pola ok. 1 – 2 s
- nałożenie stopu lutowniczego
- lutowanie potrzebuje topnika
- spoina powinna być gładka i lśniąca
- lutujemy od najmniejszych do
największych elementów

zobacz: Sparkfun tutorial https://goo.gl/8OM2ZW
NASA Student Workbook for Hand Soldering https://goo.gl/NuK80O

# Lutowanie


# Testy


- testy są ważne
- tylko jedna szansa wysłania CanSata
- testy mechaniczne i optyczne
- brak zwarć i przerw, zimnych lutów
- testy elektroniczne
- działanie samego układu
- współpraca układu z resztą systemu
- testy symulujące warunki misji

# Podsumowanie


- pomysł
- projekt
- testy prototypu
- ewentualne poprawki
- wykonanie modelu końcowego
- testy

foto: Team TechSwarm

Q&A

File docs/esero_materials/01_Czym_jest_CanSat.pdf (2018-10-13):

# CanSat - wprowadzenie


WARSZTATY CANSAT


# Czym są CanSaty?


## minisatelity?

## sondy kosmiczne?

## - eksperyment

## - metoda naukowa

## - wyzwanie

## - symulacja misji kosmicznej

# Misja CanSatów

misja podstawowa; (primary mission)

## - pomiar ciśnienia atmosferycznego

## - pomiar temperatury na zewnątrz CanSata

## - wysyłanie danych drogą radiową raz na sekundę

## - analiza danych

misja dodatkowa; (secondary mission)

# Niebo nie jest limitem* ☺

# W jakich warunkach odbywa się misja?

Dwa starty:

- testowy na dronie (lotnisko) – wysokość około 100 m
- rakieta (poligon) – 1 – 3 km (w zależności od warunków)

Krok po kroku:

1. Włączenie CanSata i włożenie do zasobnika rakiety
2. Oczekiwanie na start (zazwyczaj 2 h, maksymalnie 4 h)
3. Start rakiety, wyrzucenie CanSatów i ich powrót na ziemię
4. Poszukiwania CanSatów przez organizatorów (3 – 4 h)

(FILM Z DRONA, RAKIETY ORAZ CANSATA DEMO)

# Misja podstawowa (primary mission)

## pomiary ciśnienia, temperatury

- podstawowe dane o locie CanSata i jego zachowaniu
- maksymalna wysokość, szybkość opadania
- punkt wyjścia do innych eksperymentów

## łączność radiowa

- przekaz danych na odległość jest kluczowy w każdej misji kosmicznej
- pozwala w czasie rzeczywistym poznać stan CanSata
i jego lokalizację
- punkt wyjścia do innych eksperymentów

# Misja dodatkowa (secondary mission)

### - eksperyment definiowany przez zespół!

### - odzwierciedla ciekawość, zainteresowania uczestników lub problemy nad jakimi się zastanawiają

### - musi mieścić się w ograniczeniach regulaminowych


# Misja dodatkowa – cechy

### - realizowalność w warunkach zawodów CanSat

### - wynika z jakiegoś problemu badawczego/technicznego

### - posiada jakąś hipotezę do sprawdzenia

### - wynik nie powinien być oczywisty

### - dostosowana do możliwości drużyny

### (doświadczenie, czas, zaplecze, finanse)

## Misja dodatkowa – realizowalność i zasoby

### Realizowalność w warunkach zawodów CanSat:

- środowisko w którym będzie odbywał się eksperyment,
- niewielkie rozmiary i masa,
- ograniczony czas spadania,
- występowanie dużych przeciążeń, niestabilność lotu.

### Zasoby drużyny:

- doświadczenie w prowadzeniu złożonych projektów,
- umiejętność oszacowania czasochłonności,
- brak rezerw i planów awaryjnych.

# Misja dodatkowa – studium przypadku

Cel misji:

badanie obecności gazów w atmosferze – tlenu, dwutlenku węgla, metanu,

propanu butanu, (itd.)

- W jakim celu chcemy wykonać te konkretne pomiary?
- Redukcja zagadnień!
- Czy w atmosferze ziemskiej jest metan?

Tak, w stężeniu 1800 ppb (parts per bilion), czyli znikomym!

- Czy stężenie tlenu zmienia się na wys. 0 – 3 km?

Tak, o kilka procent - może wymagać czułych, stabilnych czujników.

# Misja dodatkowa - wybór

### Zadanie dla drużyny na najbliższy czas:

- analiza przesłanych misji (więcej o tym przy dokumentacji)

### - zawężenie tematyki

- szczegółowa analiza tematyki wybranej misji.

### Definicja misji i efekty analiz będą podstawą

### pierwszego raportu i całej pracy nad CanSatem!

# CanSat + stacja naziemna


CanSat | stacja naziemna

# Architektura CanSata

1977

system zasilania + włącznik

komputer
pokładowy

nadajnik
radiowy,
antena

czujniki misji podstawowej

eksperyment
(misja dodatkowa)

## podstawa

(CanSat bus)

## ładunek użyteczny

(payload)

system odzysku, obudowa

# Architektura CanSata


# Architektura stacji naziemnej

1977

system komunikacji; komputer PC; antena

# Architektura stacji naziemnej


1977

# Cechy systemu kosmicznego


1977

- misje kosmiczne wyróżniają się niezawodnością
- wysoki koszt, długi czas przygotowywania i tylko jedna szansa
- Zawody CanSat są tego wierną symulacją!

2004

# Niezawodny „CanSat bus”

Misja dodatkowa musi być zaprojektowana w taki sposób, aby nie zagrozić misji podstawowej!

Misja podstawowa jest kluczowa:

- dostarcza podstawowe dane o zachowaniu i działaniu CanSata,
- w przypadku niepowodzenia misji dodatkowej może pozwolić na diagnozę problemu,
- umożliwia odnalezienie CanSata,
- bez niej misja dodatkowa prawdopodobnie też się nie powiedzie.

# Niezawodny „CanSat bus”

### Jak zapewnić sukces misji CanSata?

- Misja dostosowana do możliwości drużyny i warunków
- Testowanie rozwiązań – o tym w dalszych częściach
- Analizy „czarnych scenariuszy”

# Jak zaprojektować niezawodny system?

- MISJA: transmisja wideo
- PROBLEMY: kamera pobiera dużo energii, więc jest włączana automatycznie przy starcie rakiety (czujnik przyśpieszenia)
- ARCHITEKTURA:

### system zasilania

### komputer

### pokładowy

### nadajnik radiowy

### czujniki misji podstawowej

### czujniki przyśpieszenia

### kamera

# Jak zaprojektować niezawodny system?

- PROBLEM PODCZAS MISJI

W trakcie instalacji rakiety system wykrył skok przyśpieszenia
i włączył kamerę.

Kamera rozładowała akumulator w ciągu dwóch godzin (zgodnie z przewidywaniami), dokładnie minutę przed startem.

- KONSEKWENCJE
- brak sygnału radiowego => zgubienie CanSata
- brak informacji z czujników i kamery (misja podstawowa, oraz dodatkowa zawiodły)

Dlaczego ta architektura zawiodła?

# Jak zaprojektować niezawodny system?

### system zasilania 1 (bus)

### komputer

### pokładowy

### nadajnik radiowy

czujniki misji podstawowej | kamera

### system zasilania 2 (kamera)

### czujnik przyśpieszenia

Przebudowa architektury – rozwiązanie #1

# Jak zaprojektować niezawodny system?

- MISJA: badanie zmian natężenia światła widzialnego i UV
- SPOSÓB: cyfrowy czujnik światła widzialnego, fotodioda UV
- ARCHITEKTURA OPROGRAMOWANIA:

czekaj na dane z czujnika UV; wyślij dane przez radio

### czekaj na dane z czujnika światła widzialnego

### czekaj na dane z czujników misji podstawowej

# Jak zaprojektować niezawodny system?

- PROBLEM PODCZAS MISJI:
Z powodu deszczu jeden z czujników światła zepsuł się i nie dostarczał danych.

Oprogramowanie cały czas na nie czekało, w konsekwencji nie wysyłając ani jednego zestawu danych z innych czujników.

- ROZWIĄZANIE:
Oprogramowanie powinno zignorować zepsuty czujnik i wysłać dane z reszty czujników.

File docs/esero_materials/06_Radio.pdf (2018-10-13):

# Komunikacja radiowa


WARSZTATY CANSAT


# Komunikacja radiowa

- Przesyłanie temperatury i ciśnienia z CanSata przynajmniej raz na sekundę i odbiór w stacji naziemnej – wymaganie misji podstawowej.
- Odległość pomiędzy stacją naziemną, a lądowaniem CanSatów może przekraczać 3 km! To dość duża odległość!


# Łącze radiowe


nadajnik - CanSat | odbiornik – stacja naziemna

# Radio w CanSat Kit


### Moduł radiowy

### Złącze antenowe

# Transceivery radiowe – SX1278


- Pasmo nielicencjonowane ISM 433 MHz
- LoRA®
- Simplex
- Moc 100 mW (20 dBm)
- Komunikacja z komputerem pokładowym przez magistralę SPI
- Programowanie parametrów przez komputer pokładowy – m.in. pasmo
i częstotliwość
- Dołączona biblioteka do komputera pokładowego

# Transmisja radiowa – wymagania

- Wymagane jest użycie transceivera SX1276/77/78/79 lub

RFM95/96/97/98(W) – dokładnie takiego jak w CanSat Kit

- Niezbędna jest odpowiednia konfiguracja transceivera:
- częstotliwość środkowa – unikalna dla każdej drużyny,
- pasmo sygnału – maksymalnie 125 kHz.

Konfiguracji transceivera dokonamy w prosty sposób w programie komputera pokładowego. Wszystkie ustawienia modułu radiowego muszą być takie same w CanSacie i stacji naziemnej!

## Częstotliwość środkowa, pasmo sygnału

Częstotliwość (środkowa)

Stacja radiowa Rock Radio – 103.8 MHz


Pasmo sygnału

Sygnał radiowy zawsze zajmuje pewien przedział częstotliwości – pasmo

## Częstotliwość środkowa, pasmo sygnału


# Ustawianie częstotliwości i pasma

Używane angielskie terminy: częstotliwość – frequency, pasmo – bandwidth

Radio radio(Pins::Radio::ChipSelect, Pins::Radio::DIO0,
433.0, // frequency in MHz Bandwidth_125000_Hz,
SpreadingFactor_9,
CodingRate_4_8);

Możliwe ustawienia częstotliwości: 410.0 – 525.0 MHz

Możliwe ustawienia pasma: | Bandwidth_7800_Hz | Bandwidth_41700_Hz
| Bandwidth_10400_Hz | Bandwidth_62500_Hz
| Bandwidth_15600_Hz | Bandwidth_125000_Hz
| Bandwidth_20800_Hz | Bandwidth_250000_Hz
| Bandwidth_31250_Hz | Bandwidth_500000_Hz

# Hello CanSat Kit – przez radio!

1. Do jednej płytki CanSat Kit wgraj program z przykładu

„RadioTransmitHelloCanSat” (rozdział 5.7.1 Konfiguracja nadajnika) – będzie

CanSatem

2. Do drugiej płytki wgraj „RadioReceiver” (rozdział 5.7.2 Konfiguracja

odbiornika) – będzie stacją naziemną

3. Otwórz monitor portu szeregowego, zaobserwuj pojawiające się komunikaty

– oznaczają one odebrane pakiety danych!

# Zasięg vs. szybkość transmisji

Spreading Factor – wyższa wartość zwiększa pewność transmisji, ale zmniejsza przepływność. Możliwe ustawienia: SpreadingFactor_7 - SpreadingFactor_12

Coding Rate – niższa wartość (traktuj np. 4_5 jak ułamek 4/5) zwiększa pewność transmisji, ale zmniejsza przepływność.
Możliwe ustawienia: CodingRate_4_5, CodingRate_4_6, CodingRate_4_7, CodingRate_4_8.

duża
przepływność

duża
niezawodność,
zasięg
Prędkość bitowa: R | bps | =

BW [Hz]
2

### SF ⋅ CR

## Szybkość wysyłania danych - bufor nadawczy

radio.send() | bufor
(maks. 10 ramek) | moduł radiowy

W przypadku przepełnienia bufora na Serial Monitorze zostanie wyświelone: [radio] TX buffer full!

Poprawne działanie – czyszczenie kolejki:
[radio] cleared TX queue

Aby wyłączyć wiadomości serwisowe: radio.disable_debug()

program wysyła
ramkę co 0.5 s

wysłanie ramki
trwa 1 s bufor się przepełni! brak miejsca na nowe
ramki

# Anteny

- Odpowiednio dobrane anteny zwiększą zasięg!
- Charakterystyka anteny: kierunkowa czy dookólna?
- Zakres częstotliwości – dopasowany do radia


- Wymiary anten
- Złącza

# Antena w CanSat


- CanSat – elastyczna antena z cienkiego drutu
- Monopol - kabel o długości ¼ λ ≈ 17 cm, przylutowany bezpośrednio do transceivera
- Powinna wystawać na zewnątrz
obudowy CanSata
- Najlepiej od góry / dołu
- Należy uważać na przypadkowe ekranowanie, które zmniejszy zasięg (włókno węglowe, metale)


Żyła „gorąca”

Stress relief

# Anteny – stacja naziemna


Kierunkowa - zalecana typu Yagi Złącze SMA (w zestawie)

# Zapisywanie danych z Arduino


- Serial monitor Arduino jest wystarczający do szybkiego „spojrzenia” na port
- Nie nadaje się do przechwytywania większych ilości danych

program CoolTerm

# Propagacja sygnału radiowego

- Bardzo często komunikacja zawodzi przy ziemi - strefa Fresnela


- Problemem mogą być również odbicia od budynków lub tłumienie (szczególnie problematyczne w dużych miastach)

# Testy zasięgu radiowego

- Docelowe anteny, ale nie potrzebny jest zbudowany CanSat
- Docelowy zasięg > 3 km
- Testy na ziemi, pomiędzy wysokimi budynkami lub pagórkami


# Inne transceivery i moduły radiowe

Inne moduły radiowe, transmitery TV itp. mogą zostać dopuszczone do użycia pod następującymi warunkami:

- są zgodne z obowiązującymi przepisami w Polsce,
- nie zakłócają prawidłowej pracy innych CanSatów,
- uzyskają akceptację organizatorów - waiver.


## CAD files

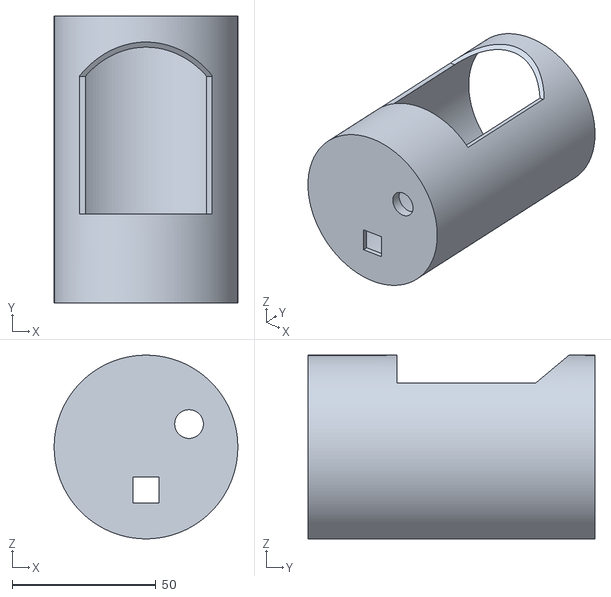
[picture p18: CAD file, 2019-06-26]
diagrams/shell/casing.stl
64.0 x 100.0 x 64.0

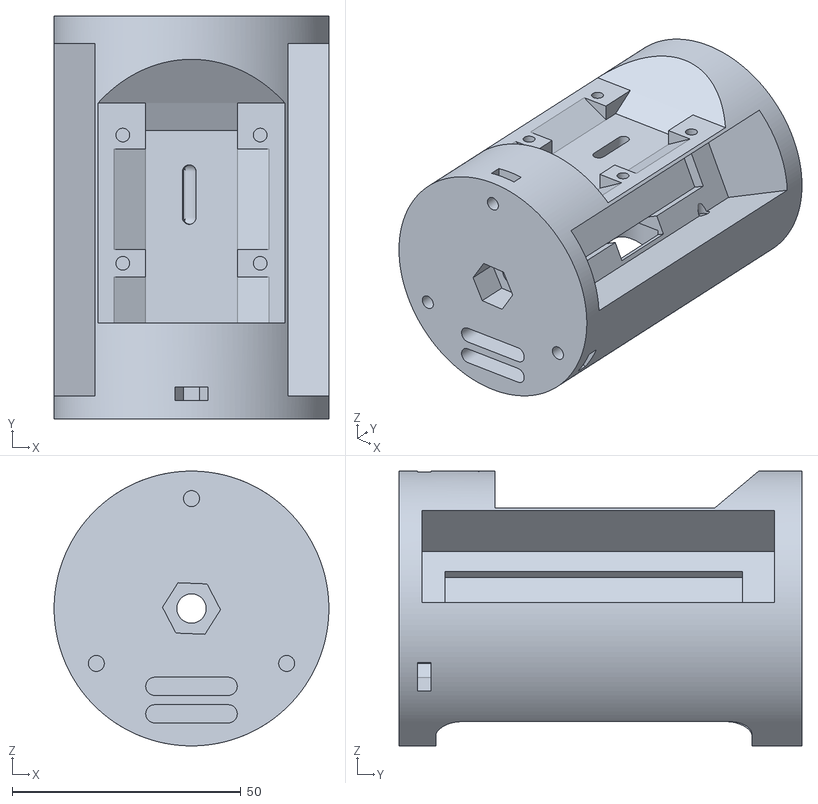
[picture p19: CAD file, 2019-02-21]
diagrams/shell/body.stl
60.0 x 88.0 x 60.0

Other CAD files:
diagrams/shell/External.f3z
diagrams/shell/Module.f3d
diagrams/shell/Puszka_final.f3z
diagrams/shell/Raport2-holes.f3z
diagrams/shell/Raport2.f3z

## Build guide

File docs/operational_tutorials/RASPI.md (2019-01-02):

# Raspbian Headless installation:

1. [Download latest raspbianhttps](://www.raspberrypi.org/downloads/)
2. Flash it on SD Card using [Etcher](https://www.balena.io/etcher/ (Windows))
3. Eject the card and plug it in again
4. Create new file in boot directory: `wpa_supplicant.conf`  
5. Write to this file:
```bash
country=PL
ctrl_interface=DIR=/var/run/wpa_supplicant GROUP=netdev
update_config=1
network={
	ssid="MyWiFiNetwork"
	psk="aVeryStrongPassword"
	key_mgmt=WPA-PSK
}
```
6. Create an empty file called `ssh` (without any extension)
7. Insert card to raspberry, wait for it to connect
8. Switch to Linux
9. Using Linux program nmap or in your router details find raspberrys IP address
10. Connect to SSH using this command:  `ssh pi@<IP>`
(replace <IP> with raspberryPi adress, e.g. `ssh pi@192.168.1.1`)
11. Login using password: raspberry
That's it!

You can exit using the command: `exit` 
And format your sd card using program DISKPART from your cmd (Windows), in cmd:
```bash
diskpart  
list disk  
select disk x  
clean  
create partition primary  
```
Links:
<https://core-electronics.com.au/tutorials/raspberry-pi-zerow-headless-wifi-setup.html>
<https://www.raspberrypi.org/documentation/remote-access/ssh/unix.md>

# Running script at boot:
```
sudo nano /etc/rc.local    
```
And add your command before *exit 0*, for instace:  
```
sudo python /home/pi/blink.py 
```

# To create a backup of SD Card:
```
sudo fdisk -l </br> 
```

will list all disks with their names and localizations  
```
sudo dd if=/dev/mmcblk0 of=~/beacan1.img
```
will copy everything to our new backup image.

from `dd` man page:
> if=file  Read input from file instead of the standard input.
> of=file  Write output to file instead of the standard output.  Any regular output file is truncated unless the notrunc conversion value is specified.  If an initial portion of the output file is seeked past (see the oseek operand), the output file is truncated at that point.

# Raspbian lifting

1. Adding a new user:
`sudo adduser username`
or new user with administrative privileges: `sudo adduser username sudo`

2. Deleting user:
`sudo userdel username`
Then you may want to delete the home directory for the deleted user account :
`sudo rm -r /home/username`

3. To modify the username of a user (must be done from another account):
`sudo usermod -l new_username old_username`

4. Changing the password:
`sudo passwd username`

5. To list all users:
`compgen -u`

6. Adding fat32 partition
`sudo fdisk /dev/mmcblk0`
By writing `p` you can display more details about your disk.
Execute command `n` to create new partition.
Select `p` (primary partition).
Select partition number, first and last sector.
Your partition has been created, now you have to change its type:
Execute command `t` and choose the partition you want to change.
Set partition id as `b` (it stands for FAT32).
Write changes: `w` and reboot.
Now FAT32 file-system can be created from command line with mkfs:
`sudo mkfs -t vfat /dev/mmcblk0pn` (where n is the partition number you have chosen) 

7. Enable I2C
`sudo raspi-config`
Choose Interfacing options, then I2C and finally Yes.

8. Enable serial port
`sudo raspi-config`
Choose Interfacing options, then Serial, answer No to the question about login shell and Yes to the question about serial hardware port.

9. Enable serial gadget
Open up the `config.txt` file that is in the SD card.
Go to the bottom and add `dtoverlay=dwc2as` the last line.
Save the config.txt file as plain text and then open up `cmdline.txt` After rootwait (the last word on the first line) add a space and then `modules-load=dwc2,g_serial`
More: https://learn.adafruit.com/turning-your-raspberry-pi-zero-into-a-usb-gadget/serial-gadget

10. Enable ethernet gadget
Open up the `config.txt` file that is in the SD card.
Go to the bottom and add `dtoverlay=dwc2as` the last line.
Save the config.txt file as plain text and then open up `cmdline.txt` After rootwait (the last word on the first line) add a space and then `modules-load=dwc2,g_ether`
In case of any troubles: https://learn.adafruit.com/turning-your-raspberry-pi-zero-into-a-usb-gadget/ethernet-gadget

11. Disable bluetooth
Go to `sudo nano /boot/config.txt`
Add below, save and close the file.
```
# Disable Bluetooth
dtoverlay=pi3-disable-bt
```
Disable related services:
```
sudo systemctl disable hciuart.service
sudo systemctl disable bluealsa.service
sudo systemctl disable bluetooth.service
```

Disable Bluetooth completely
If Bluetooth is not required at all, uninstall Bluetooth stack. It makes Bluetooth unavailable even if external Bluetooth adapter is plugged in.
```
sudo apt-get purge bluez -y
sudo apt-get autoremove -y`
```

12. Disable HDMI
`sudo nano /etc/rc.local`
Add the following lines above exit 0:
```
# Disable HDMI
/usr/bin/tvservice -o
```
13. Installing Python 3.5

a. Install the required build-tools (some might already be installed on your system).

 ```
        sudo apt-get update
        sudo apt-get install build-essential tk-dev
        sudo apt-get install libncurses5-dev libncursesw5-dev libreadline6-dev
        sudo apt-get install libdb5.3-dev libgdbm-dev libsqlite3-dev libssl-dev
        sudo apt-get install libbz2-dev libexpat1-dev liblzma-dev zlib1g-dev
 ```

   If one of the packages cannot be found, try a newer version number (e.g. ``libdb5.4-dev`` instead of ``libdb5.3-dev``).

b. Download and install Python 3.5. When downloading the source code, select the most recent release of Python 3.5, available
   on the `official site <https://www.python.org/downloads/source/>`_. Adjust the file names accordingly.

```
        wget https://www.python.org/ftp/python/3.5.2/Python-3.5.2.tgz
        tar zxvf Python-3.5.2.tgz
        cd Python-3.5.2
        ./configure --prefix=/usr/local/opt/python-3.5.2
        make
        sudo make install
```

c. Make the compiled binaries globally available.

 ```
        sudo ln -s /usr/local/opt/python-3.5.2/bin/pydoc3.5 /usr/bin/pydoc3.5
        sudo ln -s /usr/local/opt/python-3.5.2/bin/python3.5 /usr/bin/python3.5
        sudo ln -s /usr/local/opt/python-3.5.2/bin/python3.5m /usr/bin/python3.5m
        sudo ln -s /usr/local/opt/python-3.5.2/bin/pyvenv-3.5 /usr/bin/pyvenv-3.5
        sudo ln -s /usr/local/opt/python-3.5.2/bin/pip3.5 /usr/bin/pip3.5
 ```

   You should now have a fully working Python 3.5 installation on your Raspberry Pi!
d. How to change from default to alternative Python version:
```
alias python='/usr/bin/python3.5'
. ~/.bashrc
```
14. GPS setup – described [here](http://ozzmaker.com/berrygps-setup-guide-raspberry-pi/)

At the beginnig: 
```
git clone http://github.com/ozzmaker/BerryIMU.git
```
Then update software and OS
```
sudo apt-get update
sudo apt-get upgrade
sudo reboot
```
Open raspi-config and disable serial console.

To display GPS data:
```
sudo apt-get install screen
screen /dev/serial0 9600
```

Install, gpsd, gpsmon and cgps;
```
sudo apt-get install gpsd-clients gpsd -y
```

If you need to stop gpsd, you can use
```
sudo killall gpsd
```

Be default, gpsd is configured to stat at boot and run in the background. If you are fine with this, you will need to edit the config file so that gpsd uses the correct serial device.
```
sudo nano /etc/default/gpsd
```
Look for
`DEVICES=""`
and change it to
`DEVICES="/dev/serial0"`
If you want to manually run gpsd, you will need to disable it from starting at boot;
```
sudo systemctl stop gpsd.socket
sudo systemctl disable gpsd.socket
```

To force it to autostart again at boot;
```
sudo systemctl enable gpsd.socket
sudo systemctl start gpsd.socket
```

You can now use gpsmon or cgps to view GPS data.

We will be using gpspipe to capture the NMEA sentence from the BerryGPS and storing these into a file. The command to use is;
```
gpspipe -r -d -l -o /home/pi/`date +"%Y%m%d-%H-%M-%S"`.nmea
```
-r = Output raw NMEA sentences.
-d = Causes gpspipe to run as a daemon.
-l = Causes gpspipe to sleep for ten seconds before attempting to connect to gpsd.
-o = Output to file.
Now we need to force the above command to run at boot. This can be done by editing the rc.local file.
```
sudo nano /etc/rc.local
```
Just before the last line, which will be 'exit 0', paste in the below line;
`gpspipe -r -d -l -o /home/pi/`date +"%Y%m%d-%H-%M-%S"`.nmea`

15. What do we need for IMU:

```
git clone http://github.com/ozzmaker/BerryIMU.git
sudo apt-get update
sudo apt-get install i2c-tools libi2c-dev python-smbus
sudo nano /etc/modprobe.d/raspi-blacklist.conf
```
Place a hash '#' in front of blacklist i2c-bcm2708
If the above file is blank or doesn't exist, then skip the above step
You now need to edit the modules conf file.
```
 sudo nano /etc/modules
```
Add these two lines;
```
i2c-dev
i2c-bcm2708
```
Update /boot/config.txt
```
sudo nano /boot/config.txt
```
Add to the bottom;
```
dtparam=i2c_arm=on
dtparam=i2c1=on
```
More: http://ozzmaker.com/berryimu/

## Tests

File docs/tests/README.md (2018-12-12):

# Tests

This dir contains all record of conducted test, like raw data from sensors, gps dumps and so on

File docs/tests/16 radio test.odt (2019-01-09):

16.12.2018 – First LoRa Radio test

The best place where we could test the range and throughput of our radio in the center of Cracow are probably: Blonia Park and Kosciuszko Mound, so we decided to choose these spots. As a transmitter we used LoRa Ra-02 module (fitted with 17 cm long antenna) with Raspberry Pi and TTGO with LoRa onboard as receiver. To enhance the signal, our base station was equipped with 15 dB Yagi antenna (without reflector, that is important when considering the results). Before we had empirically proven that the Spreading Factor set to the value of 7 gives the best results, so we didn’t change it. The frequency band was equal to 433 MHz. We wanted to observe how radio communication changes with the changing velocity and distance.

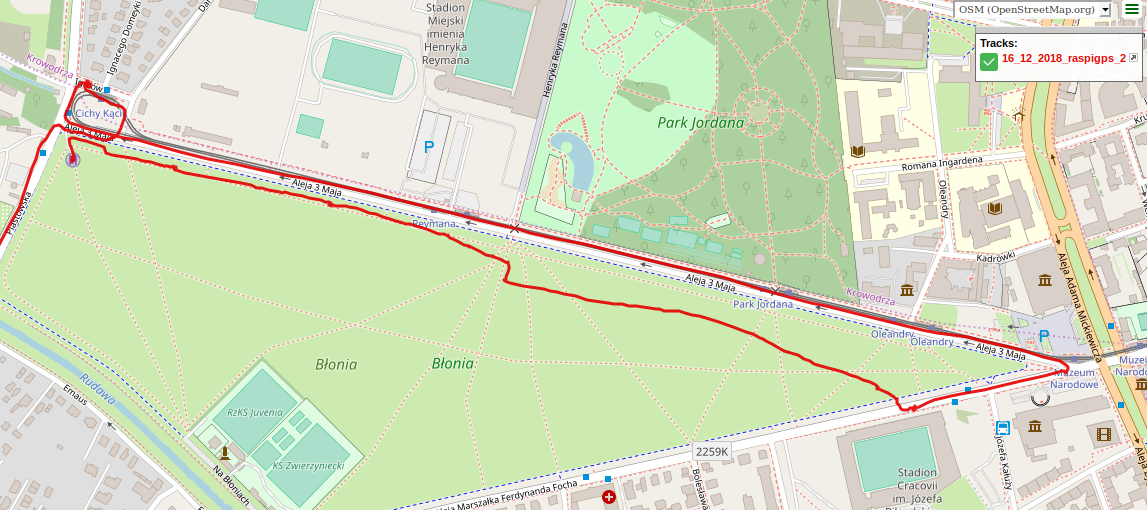
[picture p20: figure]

This table shows some correlations during the 1.2 km long walk in straight line from the base station.

Length of the packet | Delay between sending packet (ms) | Approximate distance from base station (m) | Packets per second | Percentage of received packets | Average RSSI (dBm)
30 | 300 | 0-250 | 3.28 | 98.27% | -96
20 | 300 | 250-300 | 3.26 | 99.40% | -97
20 | 500 | 300 | 2.03 | 100% | -97
10 | 500 | 300 | 1.99 | 97.30% | -99
10 | 800 | 300 | 1.33 | 81.08% | -100
10 | 300 | 300-850 | 2.81 | 85.48% | -117
10 | 500 | 850-1200 | 1.19 | 59.75% | -124

Generally, the percentage of received frames is quite satisfactory, except the last measurement. That low value was caused by losing radio connection for over a minute, about 17.4% of packets were lost then.

RSSI varied from -56 to -133 dBm, it decreases as the distance between transmitter and receiver increases, what can be observed on a chart below.

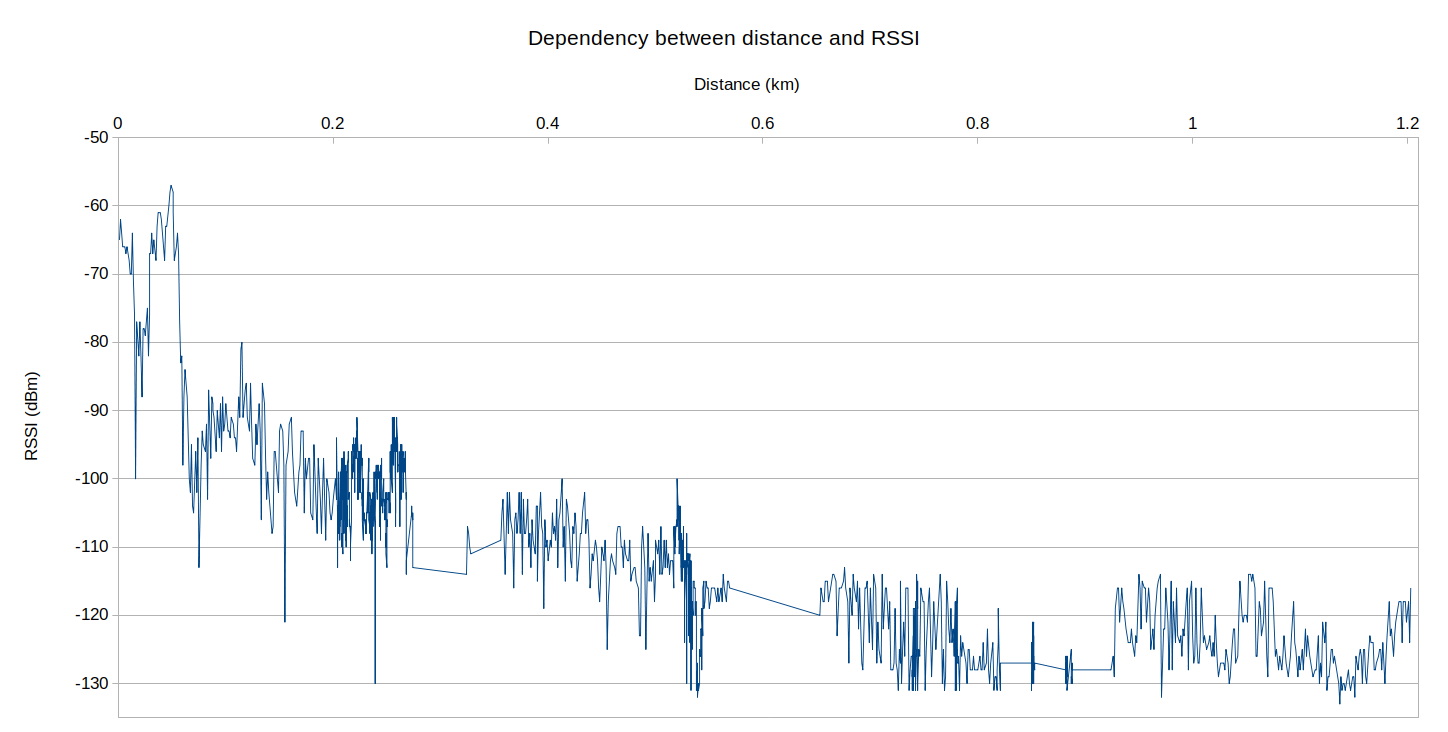
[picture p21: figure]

Then we arrived on Kosciuszko Mound and checked how does the velocity affect the communication. We were driving about a kilometer away from base station reaching the max. speed of 47.6 km/h.

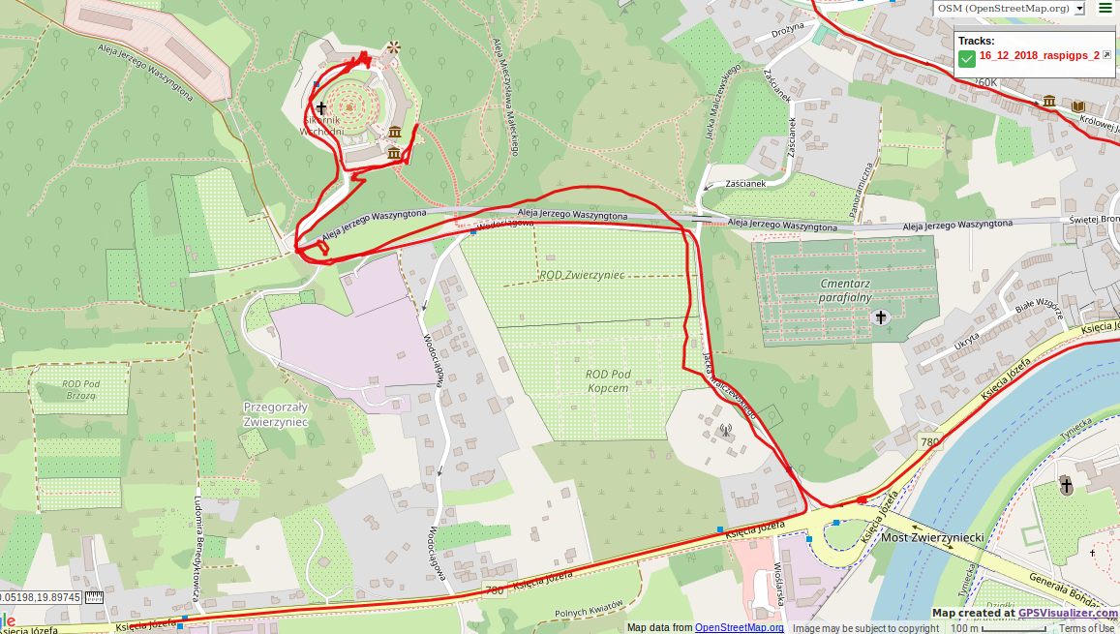
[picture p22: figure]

Some statistics:

Radio frequency: 433 MHz

Spreading factor: 7

Length of a packet: 20

Percentage of received packets: 63.69 %

Packets per second: 1.26

Average RSSI: -118 dBm

Comment: We have proven that enclosed space and velocity do not do not restrain radio contact – although it is hindered, receiving packets is possible. The percentage of received frames is low – it is strongly connected with distortions caused by trees and some buildings, enclosed space and increasing distance.

Being about 733 meters away from base station (in a straight line), we got out of the car and check the parameters. The results from that spot:

Radio frequency: 433 MHz

Spreading factor: 7

Length of a packet: 10

Percentage of received packets: 63.68 %

Packets per second: 1.26

Average RSSI: -129 dBm

Comment: Unfortunately, the number of received packets was small. Probably it was caused by too many impediments at the Fresnel zone and differences in elevation.

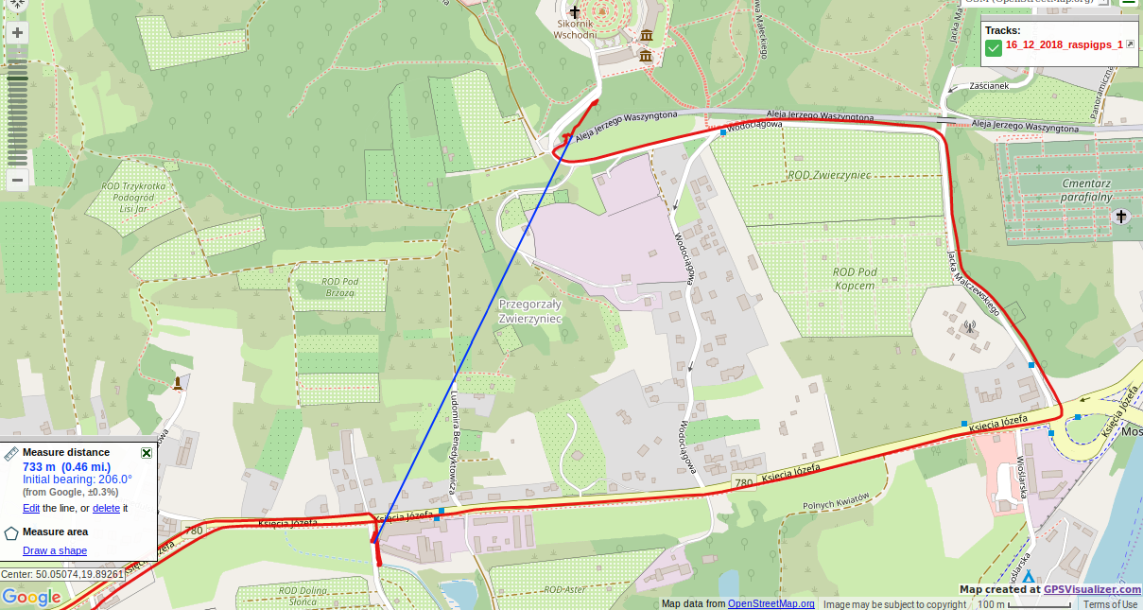
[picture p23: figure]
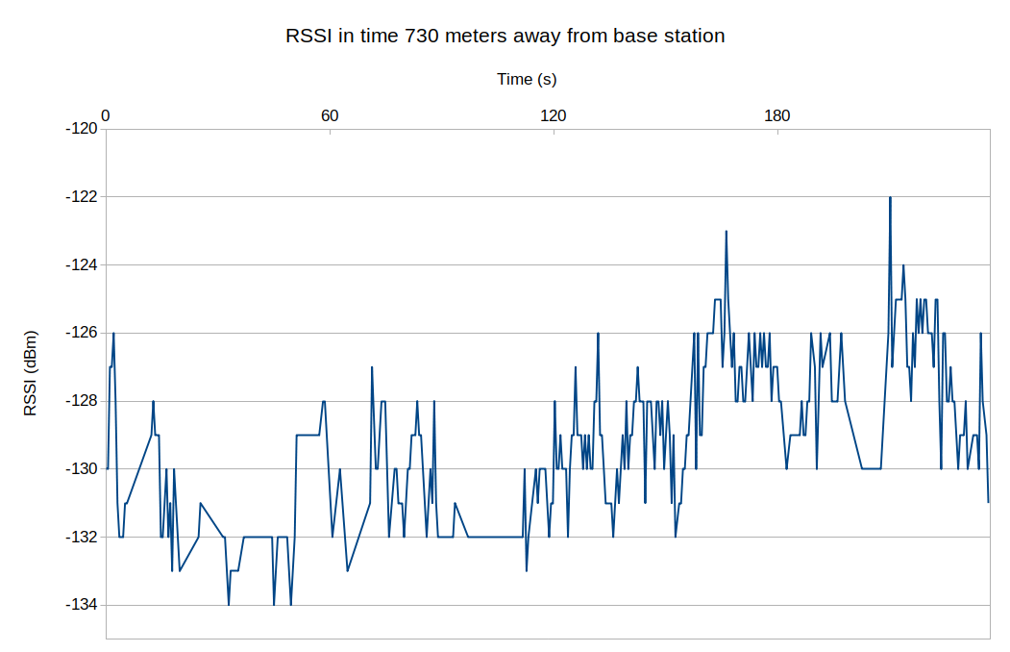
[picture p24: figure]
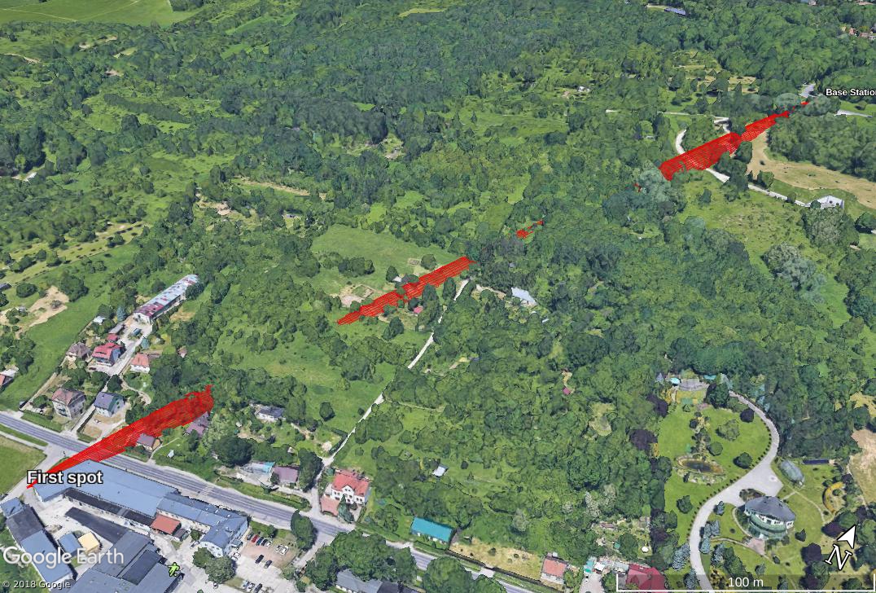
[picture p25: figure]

A visualization of Fresnel zone

As the next spot we chose the place which was about 1.6 km away from base station and we have reached contact. We were sure that we saved the log from that attempt but, regrettably, any data has been saved… One thing that we can present is the visualization of Fresnel zone. As it can be seen, it isn’t so disrupted as previous one so probably the results would be better, too.

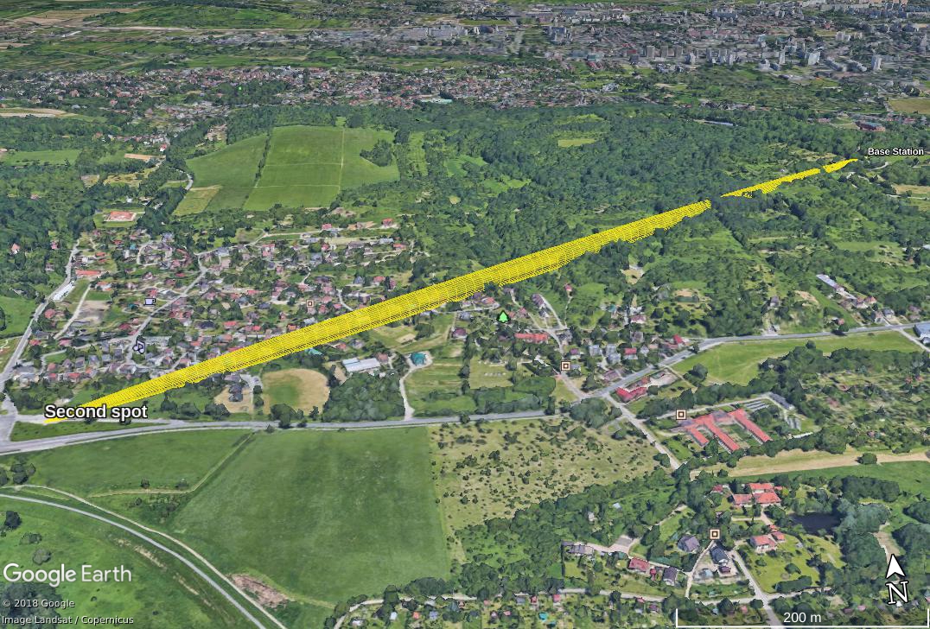
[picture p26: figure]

General conclusion:

First Radio test wasn’t bad but we expected that the results would be better. Now we now how we should deal with yagi antenna to enhance the signal – following the trajectory of transmitter movement is the key.

The correlations between the signal strength and distance/velocity were clear, so now we want to focus on the range and throughput – we should choose the place where there won’t be a lot of obstacles – it will simulate best the conditions in which our can will descending during finals (we hope so!).

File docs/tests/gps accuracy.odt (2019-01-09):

GPS accuracy

Our dear friends from Australia (Ozzmaker company to be accurate) send us wonderful BerryGPS-IMU V3. This module is so cool that when we first saw it, we knew that it must be one of the components of our can. And here it is! We’re using it as our GPS. We decided to check its accuracy compared with phone that has really precise GPS.

Let’s start with some photos:

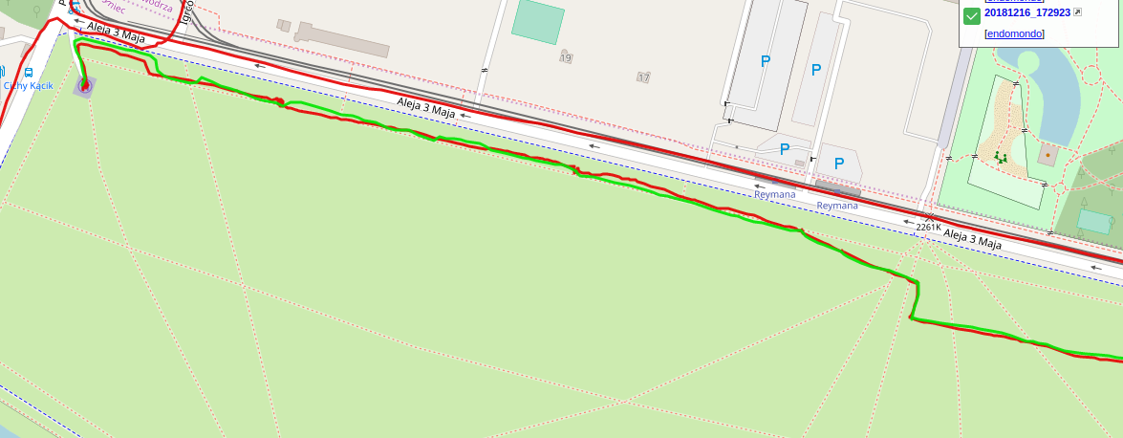
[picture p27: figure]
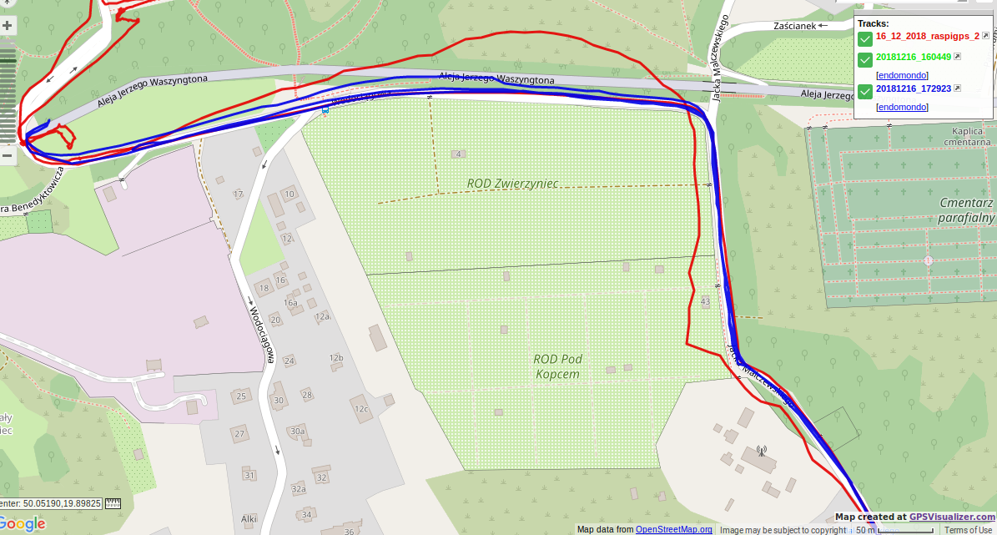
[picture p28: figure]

red line – BerryGPS-IMU, green line – phone

// the red line that is above is from another track, don’t care about it

red line – BerryGPS-IMU, blue line - phone

After having found GPS fix, the track designated by Berry IMU is almost the same as the track appointed by phone which has really precise GPS. But when Berry loses contact with some satellites, its readings start to differ from reality. During our test, the biggest measurement error was equal to around 50 m and it was noted when our module was inside a car and its velocity started to grow. After a while the number of available satellites increased so consequently the measurements became more precise again.

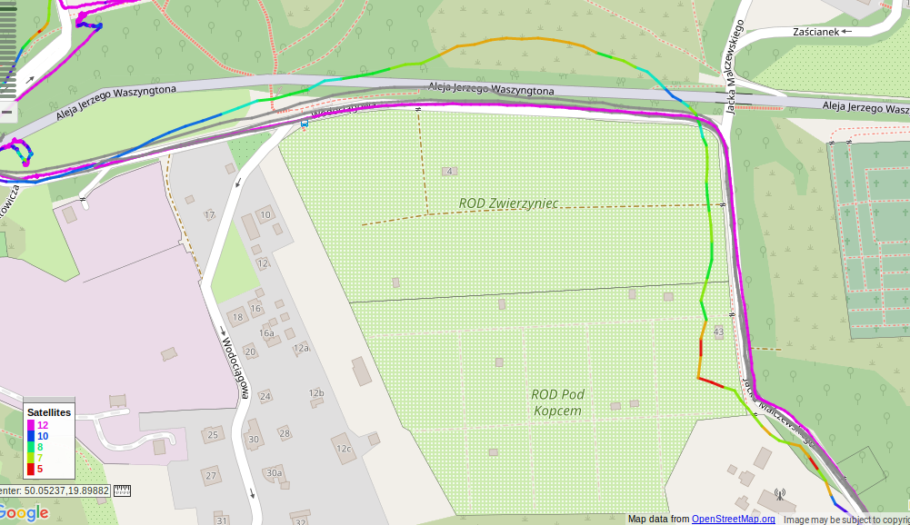
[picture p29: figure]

The higher the number of satellites, the more accurate the results.
see legend – the bottom left corner

Although sometimes BerryGPS IMU has some problems with indicating the proper route, we assume that those differences aren’t really significant . Taking into account all situations when we used this module and compared its readings to another source, we were always satisfied. We are thus ready to confide in BerryGPS’s measurements.

We have also tested how does BerryGPS perform without external antenna. Being in a car, there were a lot of problems with obtaining a fix – measurements were really deformed. But getting out of the car didn’t help much. There is only one conclusion: without external antenna the measurements are not accurate.


with external antenna

without external antenna

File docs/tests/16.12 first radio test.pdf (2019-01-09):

16.12.2018 – First LoRa Radio test

The best place where we could test the range and throughput of our radio in the center of Cracow are probably: Blonia Park and Kosciuszko Mound, so we decided to choose these spots. As a transmitter we used LoRa Ra-02 module (fitted with 17 cm long antenna) with Raspberry Pi and TTGO with LoRa onboard as receiver. To enhance the signal, our base station was equipped with 15 dB Yagi antenna (without reflector, that is important when considering the results). Before we had empirically proven that the Spreading Factor set to the value of 7 gives the best results, so we didn’t change it. The frequency band was equal to 433 MHz. We wanted to observe how radio communication changes with the changing velocity and distance.


This table shows some correlations during the 1.2 km long walk in straight line from the base station.
Length of the packet | Delay between sending packet (ms) | Approximate distance from base station (m) | Packets per second | Percentage of received packets | Average RSSI (dBm)
30 | 300 | 0-250 | 3.28 | 98.27% | -96
20 | 300 | 250-300 | 3.26 | 99.40% | -97
20 | 500 | 300 | 2.03 | 100% | -97
10 | 500 | 300 | 1.99 | 97.30% | -99
10 | 800 | 300 | 1.33 | 81.08% | -100
10 | 300 | 300-850 | 2.81 | 85.48% | -117
10 | 500 | 850-1200 | 1.19 | 59.75% | -124

Generally, the percentage of received frames is quite satisfactory, except the last measurement. That low value was caused by losing radio connection for over a minute, about 17.4% of packets were lost then.
RSSI varied from -56 to -133 dBm, it decreases as the distance between transmitter and receiver increases, what can be observed on a chart below.


Then we arrived on Kosciuszko Mound and checked how does the velocity affect the communication. We were driving about a kilometer away from base station reaching the max. speed of 47.6 km/h.


Some statistics:
Radio frequency: 433 MHz
Spreading factor: 7
Length of a packet: 20
Percentage of received packets: 63.69 %
Packets per second: 1.26
Average RSSI: -118 dBm
Comment: We have proven that enclosed space and velocity do not do not restrain radio contact – although it is hindered, receiving packets is possible. The percentage of received frames is low – it is strongly connected with distortions caused by trees and some buildings, enclosed space and increasing distance.

Being about 733 meters away from base station (in a straight line), we got out of the car and check the parameters. The results from that spot:
Radio frequency: 433 MHz
Spreading factor: 7
Length of a packet: 10
Percentage of received packets: 63.68 %
Packets per second: 1.26
Average RSSI: -129 dBm
Comment: Unfortunately, the number of received packets was small. Probably it was caused by too many impediments at the Fresnel zone and differences in elevation.


A visualization of Fresnel zone

As the next spot we chose the place which was about 1.6 km away from base station and we have reached contact. We were sure that we saved the log from that attempt but, regrettably, any data has been saved… One thing that we can present is the visualization of Fresnel zone. As it can be seen, it isn’t so disrupted as previous one so probably the results would be better, too.


General conclusion:
First Radio test wasn’t bad but we expected that the results would be better. Now we now how we should deal with yagi antenna to enhance the signal – following the trajectory of transmitter movement is the key.
The correlations between the signal strength and distance/velocity were clear, so now we want to focus on the range and throughput – we should choose the place where there won’t be a lot of obstacles – it will simulate best the conditions in which our can will descending during finals (we hope so!).

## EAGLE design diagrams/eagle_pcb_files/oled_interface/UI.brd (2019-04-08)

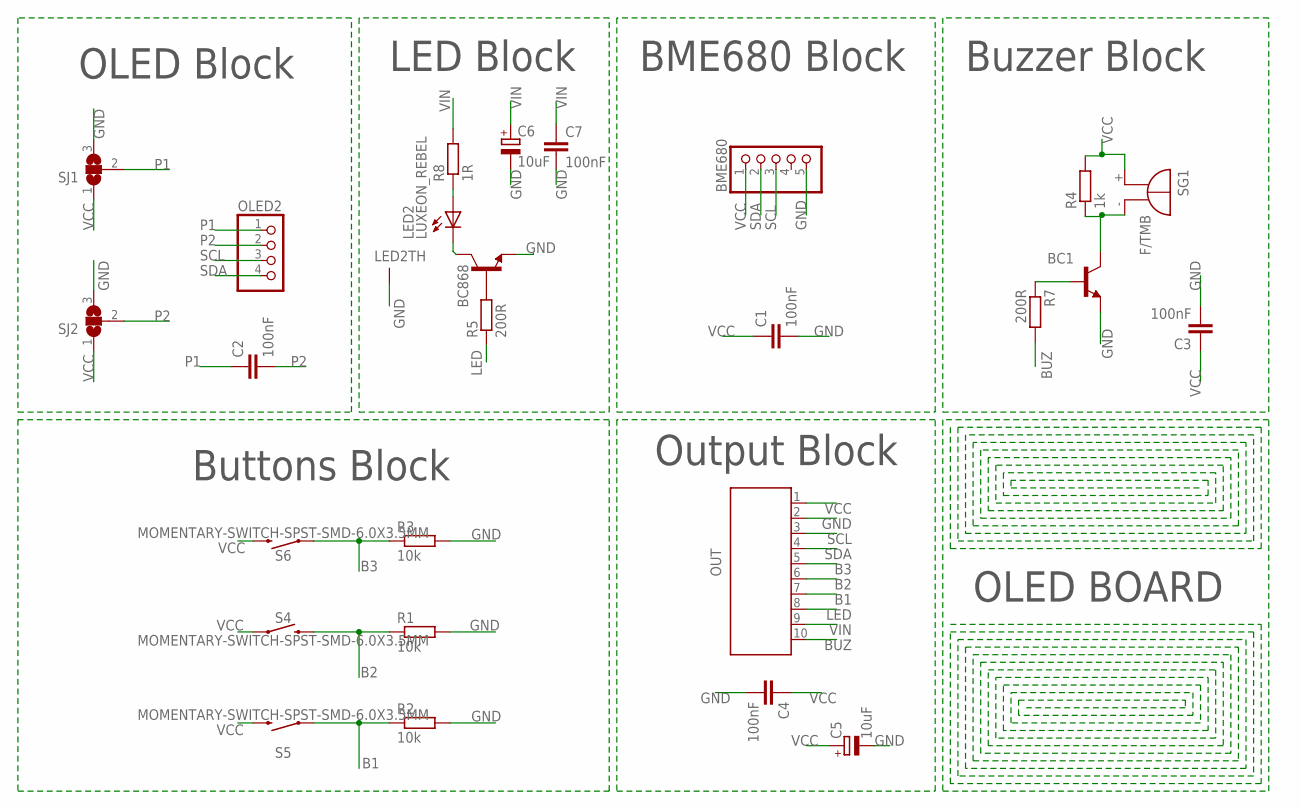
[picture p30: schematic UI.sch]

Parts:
BC1, BC868: BC868-NPN-SOT89-BCE; SOT89-BCE
BME680: PINHD-1X5; 1X05
C1, C2, C3, C7: 100nF; C0805
C4: 100nF; C1808
C5, C6: 10uF; SMC_A
LED2: LUXEON_REBEL
OLED2: PINHD-1X4; 1X04
OUT: 686110183422
R1, R2, R3: 10k; M1206
R4: 1k; M0805
R5, R7: 200R; M0805
R8: 1R; R3216
S4, S5, S6: MOMENTARY-SWITCH-SPST-SMD-6.0X3.5MM; TACTILE_SWITCH_SMD_6.0X3.5MM
SG1: F/TMB
SJ1, SJ2: SJ2W; SJ_2

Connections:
B1: OUT.7 (4), R2.1, S5.1
B2: OUT.6 (5), R1.1, S4.2
B3: OUT.5 (6), R3.1, S6.1
BUZ: OUT.10 (1), R7.2
GND: BC1.E, BC868.E, BME680.5, C1.2, C3.2, C4.2, C5.-, C6.-, C7.2, LED2.TH, LED2.TH@1 (TH), LED2.TH@2 (TH), LED2.TH@3 (TH), LED2.TH@4 (TH), OUT.2 (9), R1.2, R2.2, R3.2, SJ1.3, SJ2.3
LED: OUT.8 (3), R5.1
unnamed: LED2.A, LED2.A@1 (A), R8.1
unnamed: BC868.C, LED2.C, LED2.C@1 (C)
unnamed: BC868.B, R5.2
unnamed: BC1.B, R7.1
unnamed: BC1.C, R4.1, SG1.-
P1: C2.1, OLED2.1, SJ1.2
P2: C2.2, OLED2.2, SJ2.2
SCL: BME680.3, OLED2.3, OUT.3 (8)
SDA: BME680.2, OLED2.4, OUT.4 (7)
VCC: BME680.1, C1.1, C3.1, C4.1, C5.+, OUT.1 (10), R4.2, S4.1, S5.2, S6.2, SG1.+, SJ1.1, SJ2.1
VIN: C6.+, C7.1, OUT.9 (2), R8.2

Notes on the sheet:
OLED Block
LED Block
Buttons Block
BME680 Block
Output Block
Buzzer Block
OLED BOARD

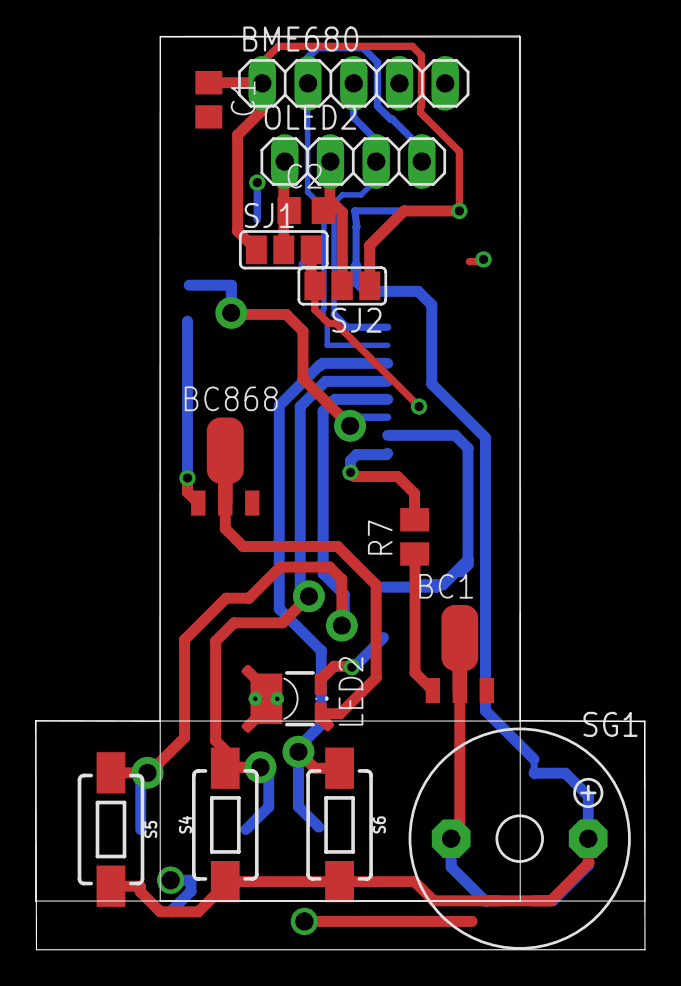
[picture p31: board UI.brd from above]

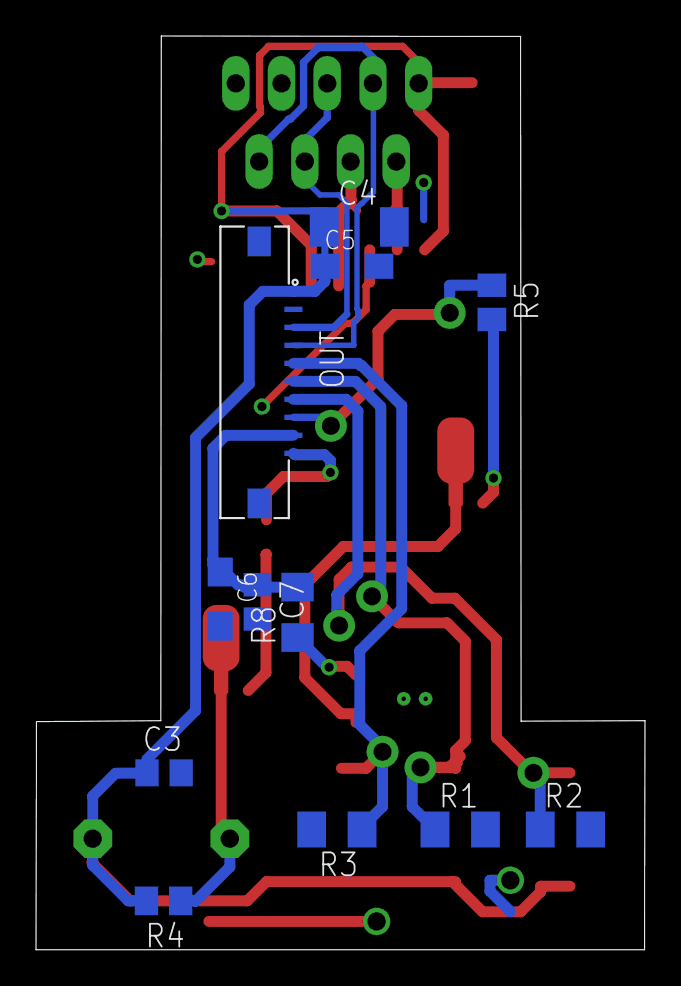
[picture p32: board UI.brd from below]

Board: 2 copper layers, 33.8 x 50.8 mm, 26 parts (12 on the bottom side), 17 nets.

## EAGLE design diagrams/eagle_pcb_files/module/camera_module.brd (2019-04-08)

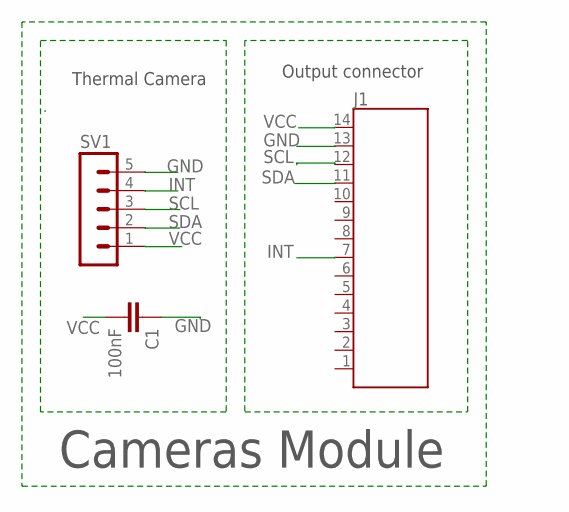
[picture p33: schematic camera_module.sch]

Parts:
C1: 100nF; C0805
J1: 686114183522
SV1: MA05-1

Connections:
GND: C1.1, J1.13 (2), SV1.5
INT: J1.7 (8), SV1.4
SCL: J1.12 (3), SV1.3
SDA: J1.11 (4), SV1.2
VCC: C1.2, J1.14 (1), SV1.1

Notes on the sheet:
Thermal Camera
Output connector
Cameras Module

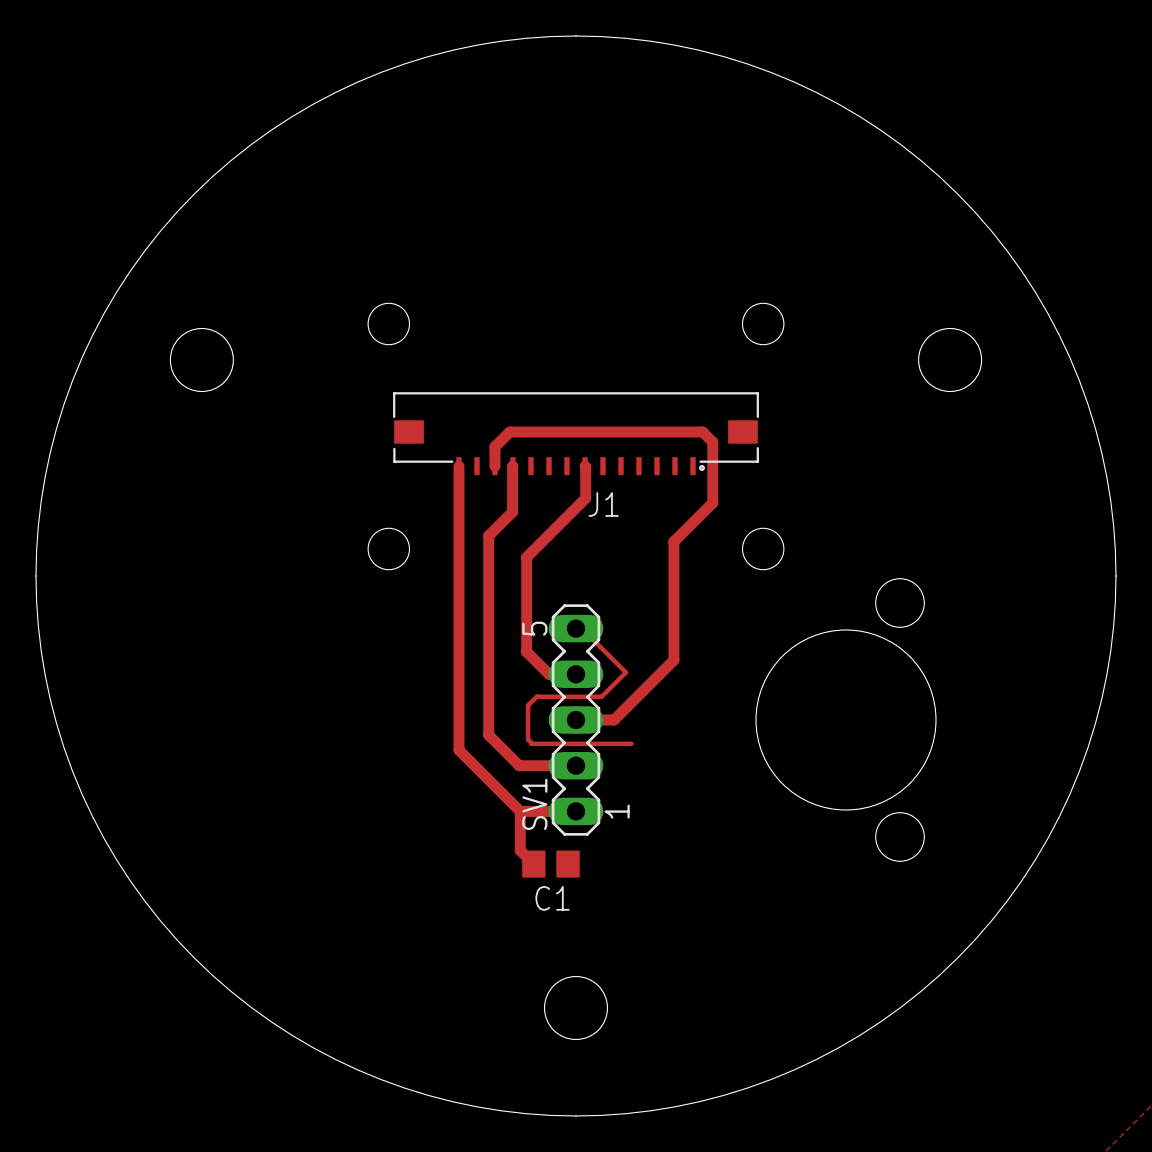
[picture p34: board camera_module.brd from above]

Board: 2 copper layers, 60.0 x 60.0 mm, 3 parts (0 on the bottom side), 5 nets.

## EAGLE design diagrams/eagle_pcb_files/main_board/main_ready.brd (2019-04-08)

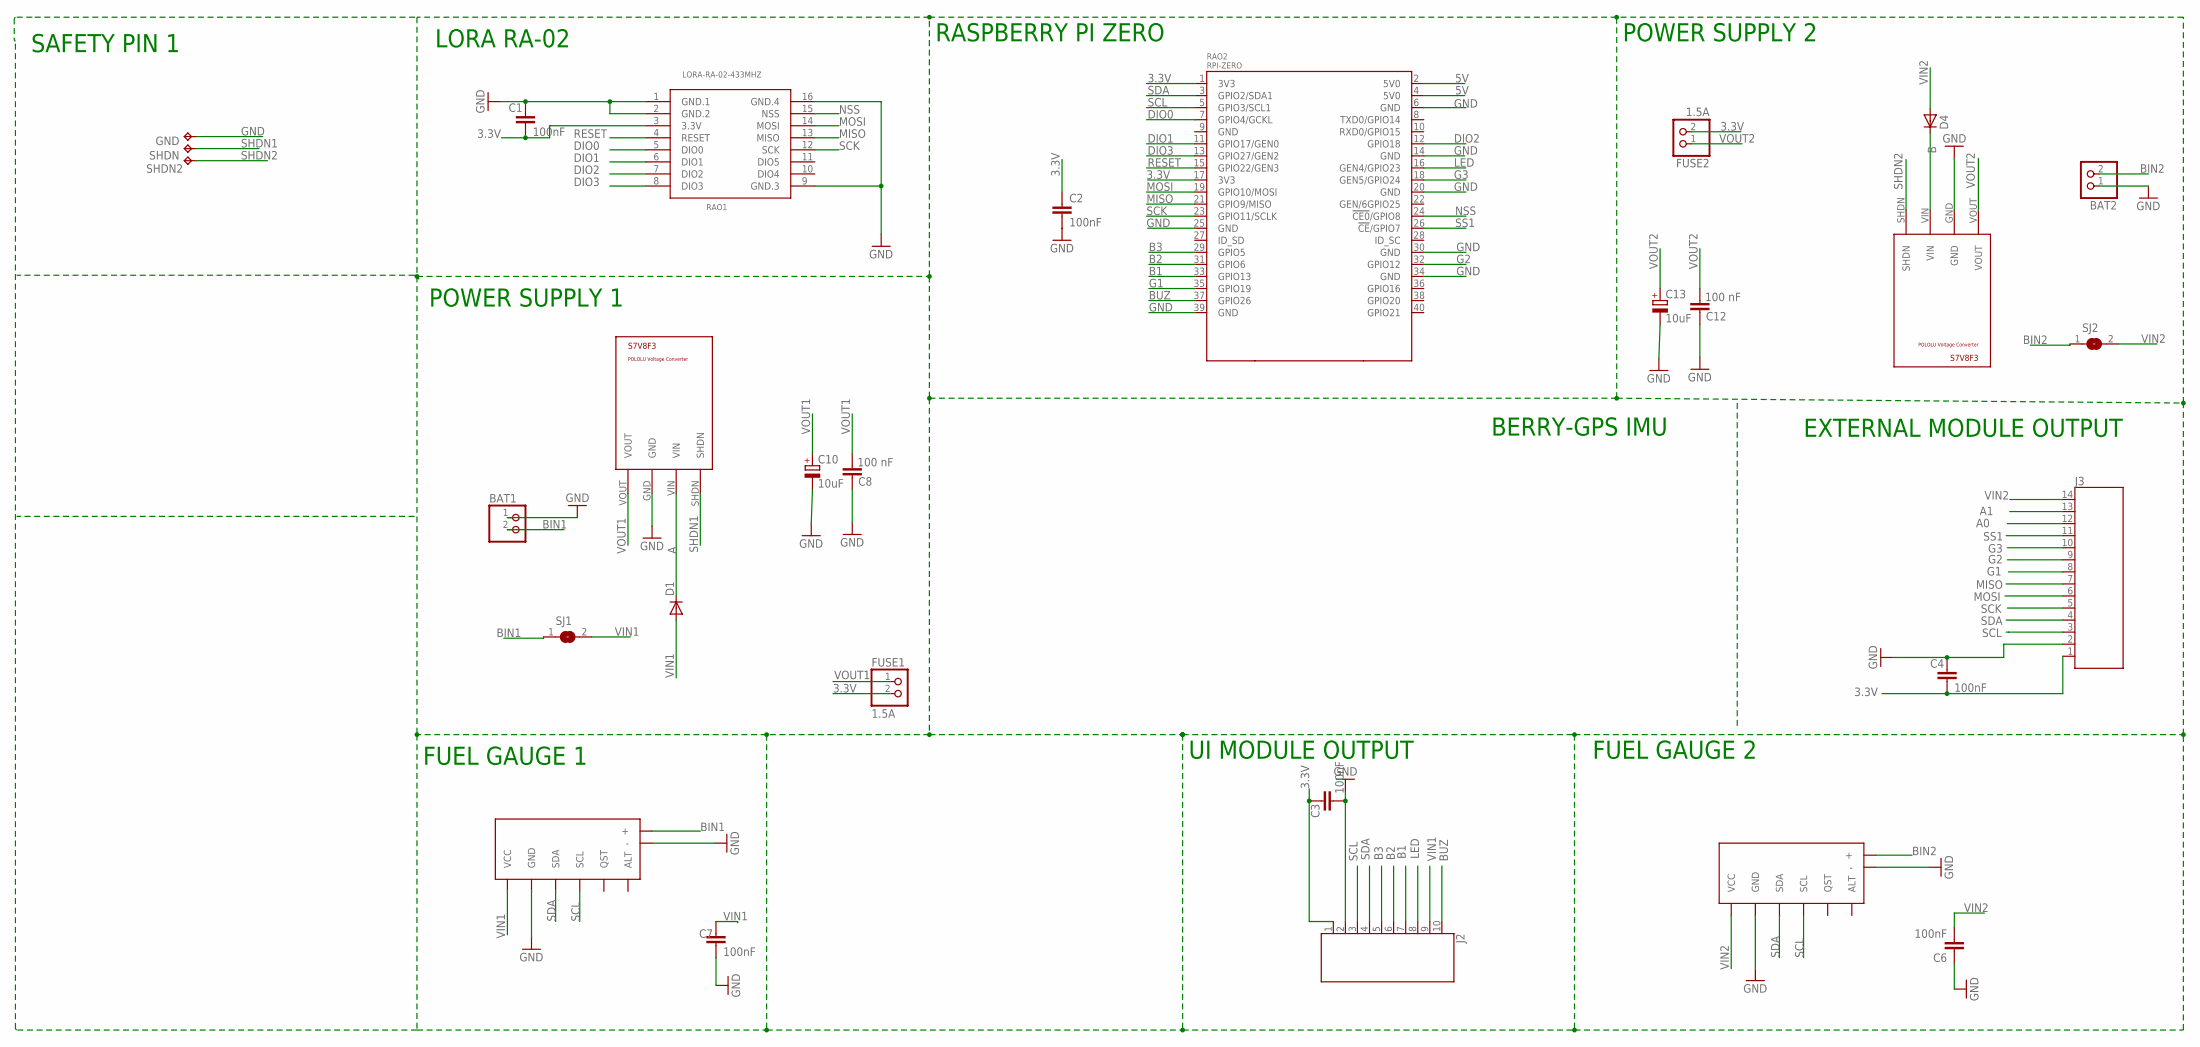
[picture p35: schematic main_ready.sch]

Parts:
BAT1, BAT2: PINHD-1X2; 1X02
C1, C2, C3, C4, C6, C7: 100nF; C0805
C8, C12: 100 nF; C0805
C10, C13: 10uF; SMC_A
D1, D4: CGRM4001-G; SOD-123_MINI-SMA
FUSE1, FUSE2: 1.5A; 1X02
GND: TPTP19R; TP19R
J2: 686110183522
J3: 686114183522
RAO1: LORA-RA-02-433MHZ; LORA-RA2-SMD
RAO2: RPI-ZERO; RASPBERRYPI_BASTELSTUBE_V13_RASPI_BOARD_B+_FULL
RAO3, RAO4: S7V8F3
SHDN: TPTP19R; TP19R
SHDN2: TPTP20R; TP20R
SJ1, SJ2: SJW
U$3, U$9: POLOLU_FUEL_GAUGEBREAKBOARD; BREAKBOARD

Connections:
3.3V: C1.2, C2.1, C3.1, C4.2, FUSE1.2, FUSE2.2, J2.1 (10), J3.1 (14), RAO1.3 (3.3V), RAO2.1 (3V3), RAO2.17 (3V3)
5V: RAO2.2 (5V0), RAO2.4 (5V0)
A: D1.C, RAO3.VIN
A0: J3.12 (3)
A1: J3.13 (2)
B: D4.C, RAO4.VIN
B1: J2.7 (4), RAO2.33 (GPIO13)
B2: J2.6 (5), RAO2.31 (GPIO6)
B3: J2.5 (6), RAO2.29 (GPIO5)
BIN1: BAT1.2, SJ1.1, U$3.+
BIN2: BAT2.2, SJ2.1, U$9.+
BUZ: J2.10 (1), RAO2.37 (GPIO26)
DIO0: RAO1.5 (DIO0), RAO2.7 (GPIO4/GCKL)
DIO1: RAO1.6 (DIO1), RAO2.11 (GPIO17/GEN0)
DIO2: RAO1.7 (DIO2), RAO2.12 (GPIO18)
DIO3: RAO1.8 (DIO3), RAO2.13 (GPIO27/GEN2)
G1: J3.8 (7), RAO2.35 (GPIO19)
G2: J3.9 (6), RAO2.32 (GPIO12)
G3: J3.10 (5), RAO2.18 (GEN5/GPIO24)
GND: BAT1.1, BAT2.1, C1.1, C2.2, C3.2, C4.1, C6.1, C7.2, C8.2, C10.-, C12.2, C13.-, GND.TP, J2.2 (9), J3.2 (13), RAO1.1 (GND.1), RAO1.2 (GND.2), RAO1.9 (GND.3), RAO1.16 (GND.4), RAO2.6 (GND), RAO2.14 (GND), RAO2.20 (GND), RAO2.25 (GND), RAO2.30 (GND), RAO2.34 (GND), RAO2.39 (GND), RAO3.GND, RAO4.GND, U$3.-, U$3.GND, U$9.-, U$9.GND
LED: J2.8 (3), RAO2.16 (GEN4/GPIO23)
MISO: J3.7 (8), RAO1.13 (MISO), RAO2.21 (GPIO9/MISO)
MOSI: J3.6 (9), RAO1.14 (MOSI), RAO2.19 (GPIO10/MOSI)
NSS: RAO1.15 (NSS), RAO2.24 (!CE0!/GPIO8)
RESET: RAO1.4 (RESET), RAO2.15 (GPIO22/GEN3)
SCK: J3.5 (10), RAO1.12 (SCK), RAO2.23 (GPIO11/SCLK)
SCL: J2.3 (8), J3.3 (12), RAO2.5 (GPIO3/SCL1), U$3.SCL, U$9.SCL
SDA: J2.4 (7), J3.4 (11), RAO2.3 (GPIO2/SDA1), U$3.SDA, U$9.SDA
SHDN1: RAO3.SHDN, SHDN.TP
SHDN2: RAO4.SHDN, SHDN2.TP
SS1: J3.11 (4), RAO2.26 (!CE!/GPIO7)
VIN1: C7.1, D1.A, J2.9 (2), SJ1.2, U$3.VCC
VIN2: C6.2, D4.A, J3.14 (1), SJ2.2, U$9.VCC
VOUT1: C8.1, C10.+, FUSE1.1, RAO3.VOUT
VOUT2: C12.1, C13.+, FUSE2.1, RAO4.VOUT

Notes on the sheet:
LORA RA-02
POWER SUPPLY 1
EXTERNAL MODULE OUTPUT
UI MODULE OUTPUT
FUEL GAUGE 2
POWER SUPPLY 2
RASPBERRY PI ZERO
FUEL GAUGE 1
SAFETY PIN 1
BERRY-GPS IMU

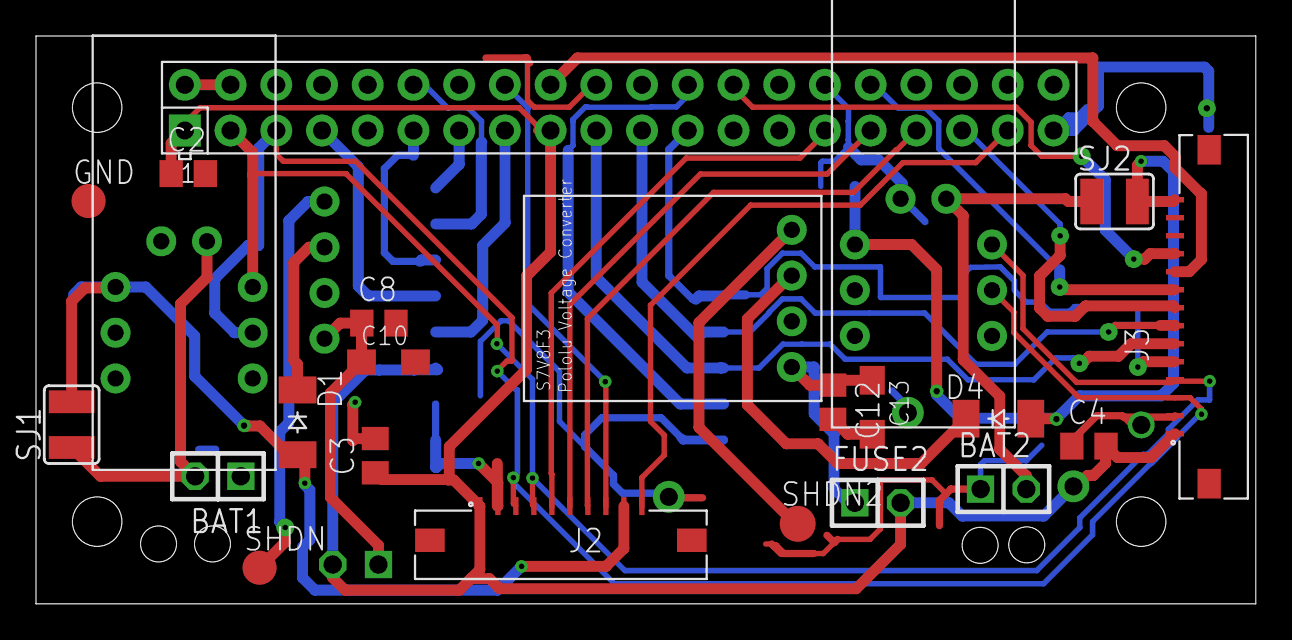
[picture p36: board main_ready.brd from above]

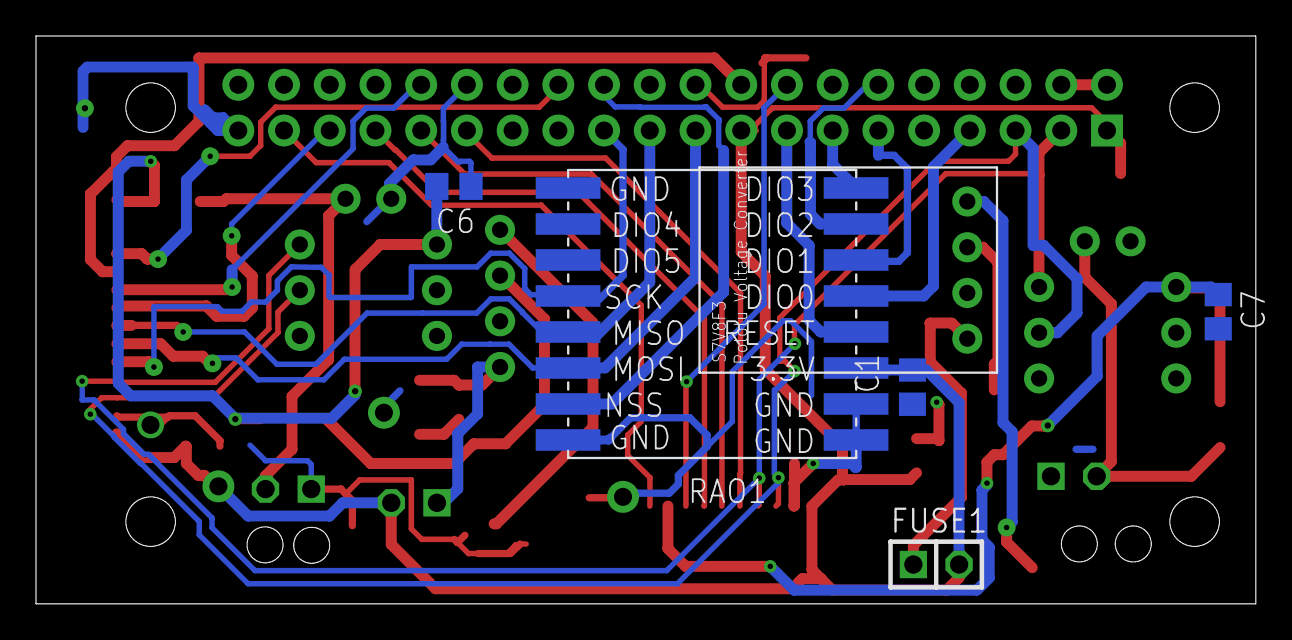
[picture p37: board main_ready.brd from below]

Board: 2 copper layers, 67.8 x 31.5 mm, 29 parts (6 on the bottom side), 33 nets.

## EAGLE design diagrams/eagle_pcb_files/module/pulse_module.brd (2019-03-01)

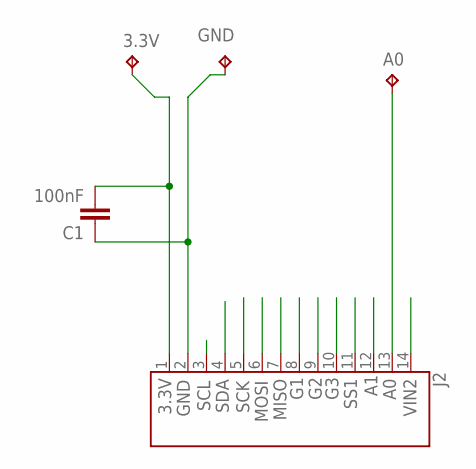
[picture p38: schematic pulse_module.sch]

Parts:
3.3V: TPTP20R; TP20R
A0: TPTP20R; TP20R
C1: 100nF; C1206
GND: TPTP20R; TP20R
J2: 686114183522

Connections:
3.3V: 3.3V.TP, C1.2, J2.1 (14)
A0: A0.TP, J2.13 (2)
A1: J2.12 (3)
G1: J2.8 (7)
G2: J2.9 (6)
G3: J2.10 (5)
GND: C1.1, GND.TP, J2.2 (13)
MISO: J2.7 (8)
MOSI: J2.6 (9)
SCK: J2.5 (10)
SCL: J2.3 (12)
SDA: J2.4 (11)
SS1: J2.11 (4)
VIN2: J2.14 (1)

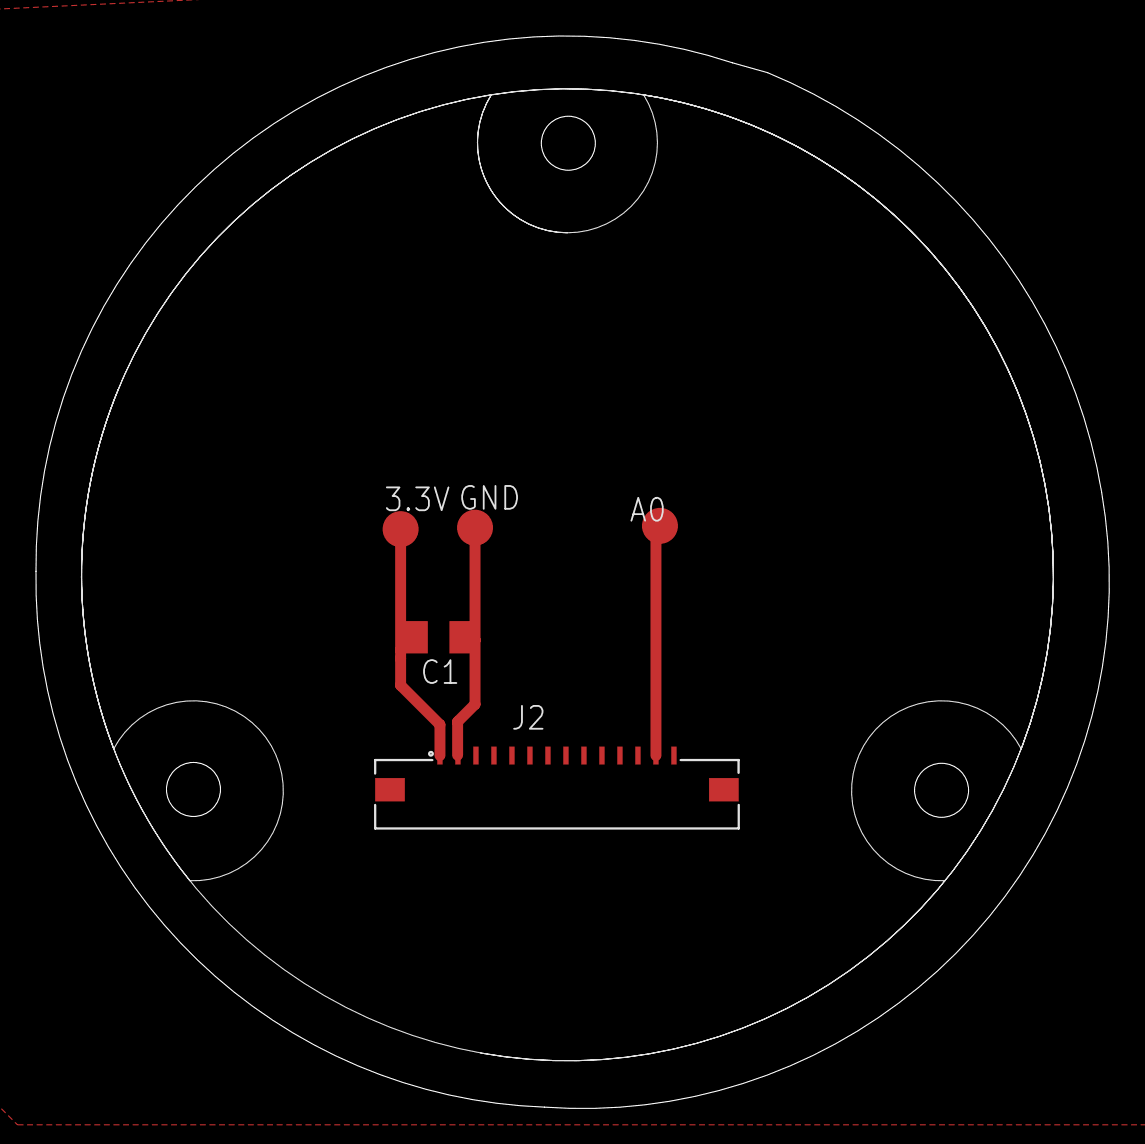
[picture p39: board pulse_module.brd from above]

Board: 2 copper layers, 59.6 x 59.6 mm, 5 parts (0 on the bottom side), 3 nets.

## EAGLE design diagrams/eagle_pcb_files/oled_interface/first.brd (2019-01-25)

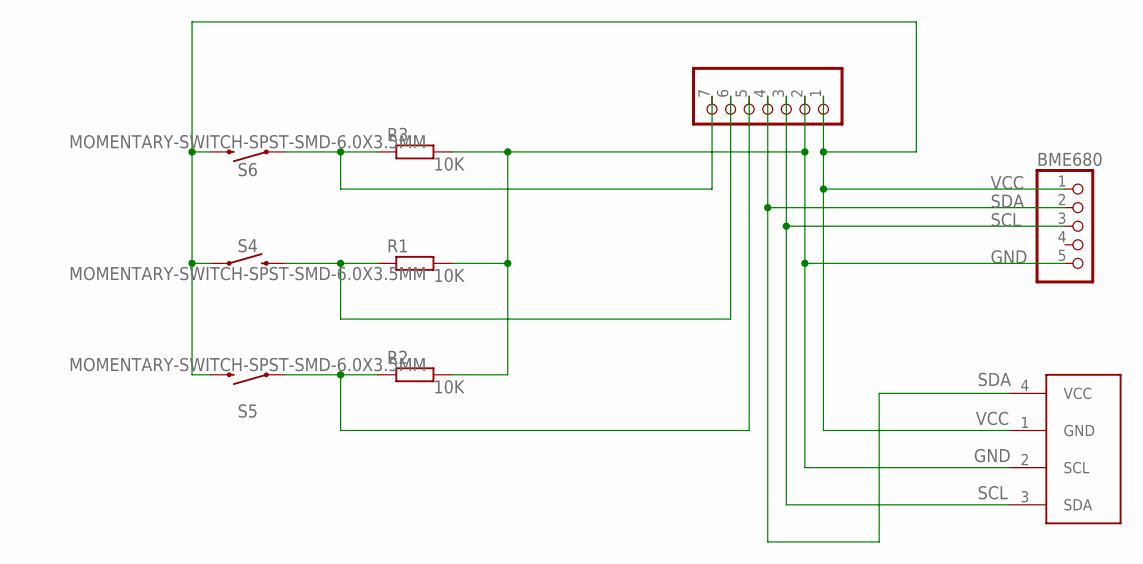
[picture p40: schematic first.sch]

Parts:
BME680: PINHD-1X5; 1X05
R1, R2, R3: R-EU_M1206; M1206
S4, S5, S6: MOMENTARY-SWITCH-SPST-SMD-6.0X3.5MM; TACTILE_SWITCH_SMD_6.0X3.5MM
SDA: PINHD-1X7; 1X07
U$1: I2C_OLED; I2C_OLED_PACKAGE

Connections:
B1: R2.1, S5.1, SDA.5
B2: R1.1, S4.2, SDA.6
B3: R3.1, S6.1, SDA.7
GND: BME680.5, R1.2, R2.2, R3.2, SDA.2, U$1.2 (SCL)
unnamed: BME680.2, SDA.4, U$1.4 (VCC)
SCL: BME680.3, SDA.3, U$1.3 (SDA)
VCC: BME680.1, S4.1, S5.2, S6.2, SDA.1, U$1.1 (GND)

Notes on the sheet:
VCC
GND
SCL
SDA

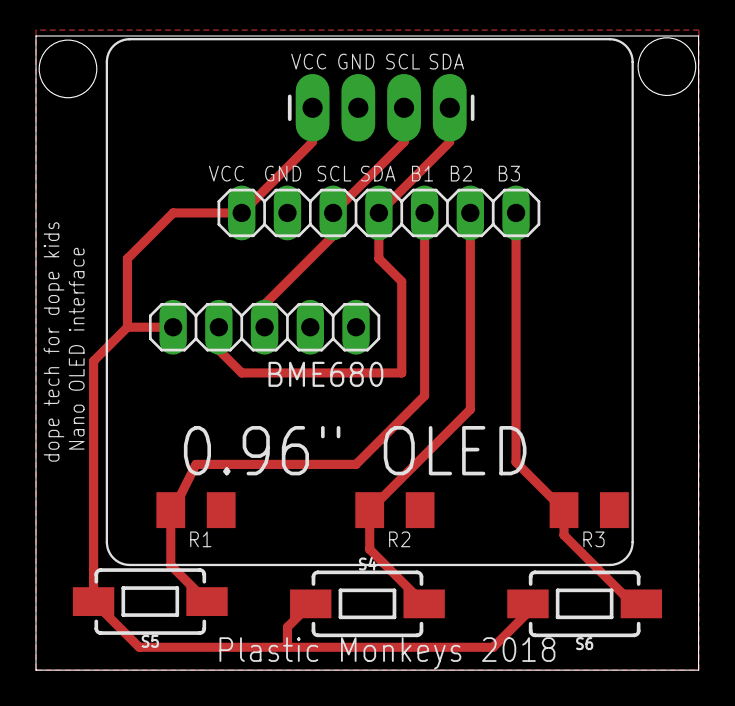
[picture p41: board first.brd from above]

Board: 2 copper layers, 36.8 x 35.2 mm, 9 parts (0 on the bottom side), 7 nets.

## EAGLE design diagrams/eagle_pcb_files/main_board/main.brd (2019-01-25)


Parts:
BAT1, BAT2: PINHD-1X2; 1X02
BC639: BCX59SMD; TO92-EBC
C1, C2, C3, C4, C5, C6, C7: C-EUC0402; C0402
D1: DIODE1206; 1206
FUSE1, FUSE2: PINHD-1X2; 1X02
LED_OUTPUT: PINHD-1X2; 1X02
R1: RESISTOR1206; 1206
RAO1: LORA-RA-02-433MHZ; LORA-RA2-SMD
RAO2: RPI-ZERO; RASPBERRYPI_BASTELSTUBE_V13_RASPI_BOARD_B+_FULL
RAO3, RAO4: S7V8F3
U$1: TYCO_8PIN_1MM_SMD; TYCO_1MM_8PIN
U$2: TYCO_12PIN_1MM_SMD; TYCO_1MM_12PIN
U$3, U$9: POLOLU_FUEL_GAUGEBREAKBOARD; BREAKBOARD
U$4, U$7, U$8: DIODE1206; 1206
U$5, U$6: SMD_COMPONENT1206; 1206

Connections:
B1: RAO2.29 (GPIO5), U$1.P$7
B2: RAO2.31 (GPIO6), U$1.P$6
B3: RAO2.33 (GPIO13), U$1.P$5
BIN1: BAT1.2, D1.P$1
BIN2: BAT2.2, U$8.P$1
DIO0: RAO1.5 (DIO0), RAO2.7 (GPIO4/GCKL)
DIO1: RAO1.6 (DIO1), RAO2.11 (GPIO17/GEN0)
DIO2: RAO1.7 (DIO2), RAO2.12 (GPIO18)
DIO3: RAO1.8 (DIO3), RAO2.13 (GPIO27/GEN2)
G1: RAO2.35 (GPIO19), U$2.P$10
G2: RAO2.32 (GPIO12), U$2.P$11
G3: RAO2.18 (GEN5/GPIO24), U$2.P$12
GND: BAT1.1, BAT2.1, BC639.E, C1.1, C2.2, C3.2, C4.2, C5.1, C6.2, C7.2, RAO1.1 (GND.1), RAO1.2 (GND.2), RAO1.9 (GND.3), RAO1.16 (GND.4), RAO2.25 (GND), RAO3.GND, RAO4.GND, U$1.P$2, U$2.P$2, U$3.-, U$3.GND, U$5.P$1, U$6.P$1, U$9.-, U$9.GND
LED: R1.P$1, RAO2.16 (GEN4/GPIO23)
MISO: RAO1.13 (MISO), RAO2.21 (GPIO9/MISO), U$2.P$6
MOSI: RAO1.14 (MOSI), RAO2.19 (GPIO10/MOSI), U$2.P$5
unnamed: BC639.B, R1.P$2
unnamed: FUSE2.2, U$6.P$2, U$7.P$1
unnamed: FUSE1.2, U$4.P$1, U$5.P$2
unnamed: BC639.C, LED_OUTPUT.1
NSS: RAO1.15 (NSS), RAO2.24 (!CE0!/GPIO8), U$2.P$8
RESET: RAO1.4 (RESET), RAO2.15 (GPIO22/GEN3)
SCK: RAO1.12 (SCK), RAO2.23 (GPIO11/SCLK), U$2.P$7
SCL: RAO2.5 (GPIO3/SCL1), U$1.P$3, U$2.P$3, U$3.SCL, U$9.SCL
SDA: RAO2.3 (GPIO2/SDA1), U$1.P$4, U$2.P$4, U$3.SDA, U$9.SDA
SS2: RAO2.26 (!CE!/GPIO7), U$2.P$9
VIN2: RAO4.VIN, U$8.P$2, U$9.+
VOUT1: FUSE1.1, RAO3.VOUT
VOUT2: FUSE2.1, RAO4.VOUT

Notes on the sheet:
LORA RA-02
POWER SUPPLY 1
LED DRIVER
EXTERNAL MODULE OUTPUT
UI MODULE OUTPUT
FUEL GAUGE 2
POWER SUPPLY 2
RASPBERRY PI ZERO
FUEL GAUGE 1

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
Board: 2 copper layers, 28 parts (8 on the bottom side), 31 nets, no tracks yet.

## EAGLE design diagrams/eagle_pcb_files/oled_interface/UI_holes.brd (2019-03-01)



Board: 2 copper layers, 39.1 x 50.7 mm, 19 parts (10 on the bottom side), 15 nets.

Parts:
B1: Buzzer; BUZZER-CCV
BME680: 1X05
C1, C2: C0805
J1: 686110183422
LED2: LUXEON_REBEL
OLED: I2C_OLED; I2C_OLED_PACKAGE
Q1, Q2: BCX59SMD; TO92-EBC
R1, R2, R3, R5, R6: 10k; M1206
R4: 10R; M1206
R7: 200R; M1206
S4, S5, S6: MOMENTARY-SWITCH-SPST-SMD-6.0X3.5MM; TACTILE_SWITCH_SMD_6.0X3.5MM

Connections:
B1: J1.7, R2.1, S5.1
B2: J1.6, R1.1, S4.2
B3: J1.5, R3.1, S6.1
BUZ: J1.10, R6.1
GND: BME680.5, C1.1, C2.1, J1.2, OLED.2, Q1.E, Q2.E, R1.2, R2.2, R3.2
LED: J1.8, R5.1
unnamed: LED2.A, LED2.A@1, R4.1
unnamed: LED2.C, LED2.C@1, Q1.C
unnamed: Q1.B, R5.2
unnamed: Q2.B, R6.2
SCL: BME680.3, J1.3, OLED.3
SDA: BME680.2, J1.4, OLED.4
TH: LED2.TH, LED2.TH@1, LED2.TH@2, LED2.TH@3, LED2.TH@4
VCC: BME680.1, J1.1, OLED.1, S4.1, S5.2, S6.2
VIN1: C1.2, C2.2, J1.9, R4.2, R7.2

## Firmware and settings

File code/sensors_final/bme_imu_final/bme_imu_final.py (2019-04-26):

import sys
import smbus2
import bme280
import configparser
from time import sleep, time

config_file = sys.argv[1]
config = configparser.ConfigParser()
config.read(config_file)

address = int(config['SETTINGS']['address'], 16)
log_path_temp = config['PATHS']['temperature_log']
log_path_pres = config['PATHS']['pressure_log']
sleep_time = float(config['SETTINGS']['sleep_time'])

i2c = smbus2.SMBus(1)

while True:
    try:
        data = bme280.sample(i2c, address)
        t = int(round((data.temperature+25)*10)) # range(-25, 38) delta=0.1
        p = round((data.pressure-450)*10) # range(450, 1090) delta=0.1
        timestamp = round(time())
        #print("BMP280 Pressure: {0}".format(p))
        #print("BMP280 Temp: {0}".format(t))
        output_t = ('{} {}\n').format(timestamp,t)
        output_p = ('{} {}\n').format(timestamp,p)
        tf = open(log_path_temp, "a")
        tf.write(output_t)
        tf.close()
        pf = open(log_path_pres, "a")
        pf.write(output_p)
        pf.close()
        sleep(sleep_time)
    except Exception:
        sleep(sleep_time)

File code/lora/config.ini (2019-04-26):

[util]
rx_log = /home/pi/lora_logs/rx.txt
status_log = /home/pi/lora_logs/status.txt
cmd_file = /home/pi/lora_logs/cmd.txt
images = /home/pi/images
thermal = /home/pi/thermal
logging = /home/pi/lora_logs/logs/

[data]
mg1 = /home/pi/lora_logs/mg1
mg2 = /home/pi/lora_logs/mg2

[params]
up_packet_length = 11
down_packet_length = 25
cmd_length = 10
max_backread = 5
max_buffer_length = 50
tx_time = 0.11
rx_time = 0.14
thermal_height = 32
thermal_width = 24

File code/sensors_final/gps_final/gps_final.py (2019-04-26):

import serial
import sys
import pynmea2
import configparser
from time import sleep, time

config_file = sys.argv[1]
config = configparser.ConfigParser()
config.read(config_file)

port_path = config['SETTINGS']['uart_port_path']
uart_baudrate = int(config['SETTINGS']['uart_baudrate'])
uart_timeout = float(config['SETTINGS']['uart_timeout'])
sleep_time = float(config['SETTINGS']['sleep_time'])

latitude_log = config['PATHS']['gps_latitude_log']
longitude_log = config['PATHS']['gps_longtitude_log']
altitude_log = config['PATHS']['gps_altitude_log']
timestamp_log = config['PATHS']['gps_timestamp_log']

serialPort = serial.Serial(port_path, baudrate=uart_baudrate)

def parseGPS(line):
    if line.find("GGA") > 0:
        #print(line)
        msg = pynmea2.parse(line)
        #tim = (msg.timestamp.hour * 60 + msg.timestamp.minute) * 60 + msg.timestamp.second
        lat = round((msg.latitude+90)*100000) if msg.latitude is not None else 0
        lon = round((msg.longitude+180)*100000) if msg.longitude is not None else 0
        alt = round(msg.altitude) if msg.altitude is not None else 0
        unix_timestamp = round(time())

        file_dict = {
            'latitude': [latitude_log, lat],
            'longitude': [longitude_log, lon],
            'altitude': [altitude_log, alt] #,
            #'timestamp': [timestamp_log, tim]
        }

        for type in file_dict:
            open_file = open(file_dict[type][0], "a")
            open_file.write(('{} {}\n').format(unix_timestamp,file_dict[type][1]))
            open_file.close()


while True:
    try:
        line = serialPort.readline().decode('utf-8')
        parseGPS(line)
        sleep(sleep_time)
    except Exception as ex:
        #print(ex)
        sleep(sleep_time)

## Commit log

2018-11-18 Add programs for Ra-02 sender (Arduino Micro), TTGO Receiver, TTGO Display Test
2018-11-18 Fixed bug causing Arduino Micro to freeze until Serial Monitor was opened
    [Arduino_Micro_Sender.ino]
2018-11-18 update readme.md in PDR-Cad-Drawings
2018-11-20 Add Arduino Sender-Receiver. Two-way communication stable
2018-11-20 Fixed a bug causing statistic to return false values
    [Arduino_Micro_Sender_Receiver.ino, TTGO_Sender_Receiver.ino]
2018-11-24 Raspberry Pi Setup Notes
    Some information about Raspbian setup.
2018-11-24 Add led.py file
2018-11-24 Add led_button.py
2018-11-24 Add i2cpressure.py
2018-11-25 Add button_shutdown.py. This file runs on boot and provides soft shutdown
2018-11-25 Added w1temperature.py. Changed i2cpressure.py to only read once
2018-12-02 Small typo fixes in ttgo tests
    [Arduino_Micro_Sender.ino]
2018-12-02 Revert "Some minor fixes"
    This reverts commit fc6940eb0fbb5beb42eb2d8d6aa745561c27a437.
    [TTGO_OLED.ino]
2018-12-02 Revert "My own Lora Tests code for new TTGOs"
    This reverts commit c04bb0b3a94ab2ccd09a2299bc5c3c828b53e1e0.
    [Arduino_Micro_Sender.ino, TTGO_OLED.ino]
2018-12-08 DS18B20 now uses provided lib. Reworked allsensors.py
    [allsensors.py, button_shutdown.py, led.py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]
2018-12-08 Created separate file for IMU BME280. Added GPS to allsensors.py
2018-12-09 replace tabs with spaces
    [allsensors.py, button_shutdown.py, gps.py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]
2018-12-15 First update of TX.ino
    Serial Rate defined on top
    Special Led class - didn't manage to learn how to create a separate library
    Removed weird delay
    [TX.ino]
2018-12-15 Major fix to RX.ino
    Changed this weird u8x8 to OLED
    Created some math functions to calculate data speed and percentage of correct packets
    New `readData` function
    bools are now `true/false`
    [RX.ino]
2018-12-19 adding OLED interface project
    crazy stuff
    [first.brd, first.sch]
2018-12-20 Upgraded OLED Board
    New board for fast manufacturing
    [first.brd, first.sch]
2018-12-23 Added voltage regulator schematic
2018-12-24 first bunch of our eagle libraries
    BERRYIMU - BerryGPS-IMU v3
    Connector-FFC - 10 pin 0.5mm connector
    DIYMall_OLED - Oled screen (wrong pinout, gonna change it)
    LikeCircuit - Ra02
    pinhead - goldpins
    RPI-Zero - Raspberry Pi Zero
    switch-tact - all kind of small switches and buttons
2018-12-24 New Pololu Voltage Converter Library
    Includes two voltage converters:
    S7V8F3
    S9V11F3S5
2018-12-25 Added support for buzzer
    [led_button.py]
2018-12-25 Add current_sensor Arduino code which measures current flowing through Pi
2018-12-27 New Library for Bigger Tact Switches
2018-12-27 New Buttons Pads
    previous was too small for our buttons
    [first.brd, first.sch]
2019-01-02 Our main CanSat Board
    yee help me pls guys
    [main.brd, main.sch]
2019-01-03 Temporary version of main board
    :')
    [main.brd, main.sch]
2019-01-03 Bit better schematic
    more readable
    [main.sch]
2019-01-03 Better Schematic was so good, i've released sequel
    better schematic
    [main.sch]
2019-01-03 jeez another schematic
    Added fancy aesthetics
    [main.sch]
2019-01-08 Ready to fly database
    just insert new questions, command to do that is commented in simple.py
2019-01-10 Diagram of our new main board idea
2019-01-25 Fusion360 Can Design by Janek
    [Raport2.f3z]
2019-01-25 move things around, cleanup
    [first.brd, first.sch, main.brd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]
2019-01-25 move things in diagrams
    [Raport2.f3z]
2019-01-25 clean things in eagle schematics
2019-01-25 Added space for module. Resized rod. Moved battery space down
    [Raport2.f3z]
2019-01-26 Added more space inside, module screw holes
    [Raport2.f3z]
2019-01-29 Add module.f3d
    [Module.f3d]
2019-01-31 Broadened screw and nut holes. Fixed leak to main rod. Remade cable hole to OLED board
    [Raport2.f3z]
2019-02-02 Applied suggestions. Added Raspi screw holes
    [Raport2.f3z]
2019-02-02 Added OLED scerw holes. Added safety pin hole
    [Raport2.f3z]
2019-02-02 Remade front panel to match OLED
    [Raport2.f3z]
2019-02-16 Add first brd files
    [module.brd, module.sch]
2019-02-16 Brd of main board finally on board
    [main_ready.brd, main_ready.sch]
2019-02-16 legit (I hope so) version
    [UI.brd, UI.sch]
2019-02-17 small fixes, 100pF -> 100nF, tht cap to smd cap, mounting holes, round dimension, one sided instead of two sided, gnd plane
    [module.brd, module.sch]
2019-02-17 GND plane, add 100nF cap
    [pulse_module.brd, pulse_module.sch]
2019-02-21 wider holes in body stl
    [Raport2.f3z, body_v3.stl]
2019-02-21 make routing in UI more home-made-possible
    [UI.brd, UI.sch]
2019-02-22 Some features added
    [module.brd]
2019-02-22 Add excternal casing CAD
    [External.f3z]
2019-02-22 Add external casing CAD model
    [External.f3z]
2019-02-23 New MergeBlock
    What's new:
    - You can pass your config file as an argument
    - The output is a dict
    - You can turn off text packets in config file
    - All logs can have one int before reading - for example number of a reading, merge block will ignore it
    - snaek_case
    - You can define your sensors' names in the config file
    - some minor fixes
2019-02-23 New config and sample foos
2019-02-24 Main board with wider routes and slightly less vias
    [main_ready.brd]
2019-02-24 UI board with 0805 capacitors & sparkfun's buzzer
    Versions with and without mounting holes
    [UI_holes.brd, UI_new.brd]
2019-02-24 prepare main board for production
    [main_ready.brd, main_ready.sch]
2019-02-24 generated gerbers
    [copper_bottom.gbr, copper_top.gbr, gerber_job.gbrjob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]
2019-03-03 Applied suggestions regarding PCB board spaceand some other stuff
    [Raport2-holes.f3z]
2019-03-03 shdn -> pull up, more place for components
    [main_improved.brd]
2019-03-06 OLED pins gnd and vcc changed
    [UI_gnd-vcc.brd]
2019-03-10 Add hopefully final model of cansat
    [Puszka_final.f3z]
2019-03-14 mirrored pins
    [module2.0.brd]
2019-03-21 New Software Diagram
    added Grafana part
    added Cameras
2019-04-03 make board-schematic consistent
    [body_v3.stl, main_ready.brd, main_ready.sch]
2019-04-03 remove res from safetypin, fix fuel gauge circuit, add jumper to ommit fuel gauge
    [main_ready.brd, main_ready.sch]
2019-04-04 pulse module board with adc
    [pulse_module.brd, pulse_module.sch]
2019-04-04 remove adc from main board
    [main_ready.brd, main_ready.sch]
2019-04-06 oled ready for production
    [UI.brd, UI.sch]
2019-04-06 camera module ready for production
    [camera_module.brd, camera_module.sch, module.brd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]
2019-04-06 remove ambiguous files from schematics
    [module2.0.brd, sketch_module.brd]
2019-04-06 small change to pulse module
    [pulse_module.brd]
2019-04-07 main board ready for production
    [main_ready.brd, main_ready.sch]
2019-04-07 cleanup redundant brd files
    [UI_gnd-vcc.brd, main_improved.brd]
2019-04-07 cleanup unnecessary brd files
    [body_v3.stl, sketch_module.brd]
2019-04-14 Fixed old git mistakes...
    [LoRa_Slave.ino, base_parser.py, base_sender.py]
2019-04-16 Addressed some issues to lora.py
    [config.ini]
2019-04-17 Sample Config File for Command_Block
2019-04-23 Add Led_block
2019-04-24 Resolved all issues in baseParser.py
    [base_parser3.py]
2019-04-24 Resolved issues in lora_base.ino
    [lora_base.ino]
2019-04-25 add accelerometer_block
2019-04-25 Add buzzer_block
    haha i want to sleep
    [buzzer.py, config.ini]
2019-06-26 shell stls
    [body.stl, casing.stl]

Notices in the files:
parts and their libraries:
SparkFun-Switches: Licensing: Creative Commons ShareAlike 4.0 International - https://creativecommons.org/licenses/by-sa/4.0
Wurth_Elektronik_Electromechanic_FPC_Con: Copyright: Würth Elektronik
